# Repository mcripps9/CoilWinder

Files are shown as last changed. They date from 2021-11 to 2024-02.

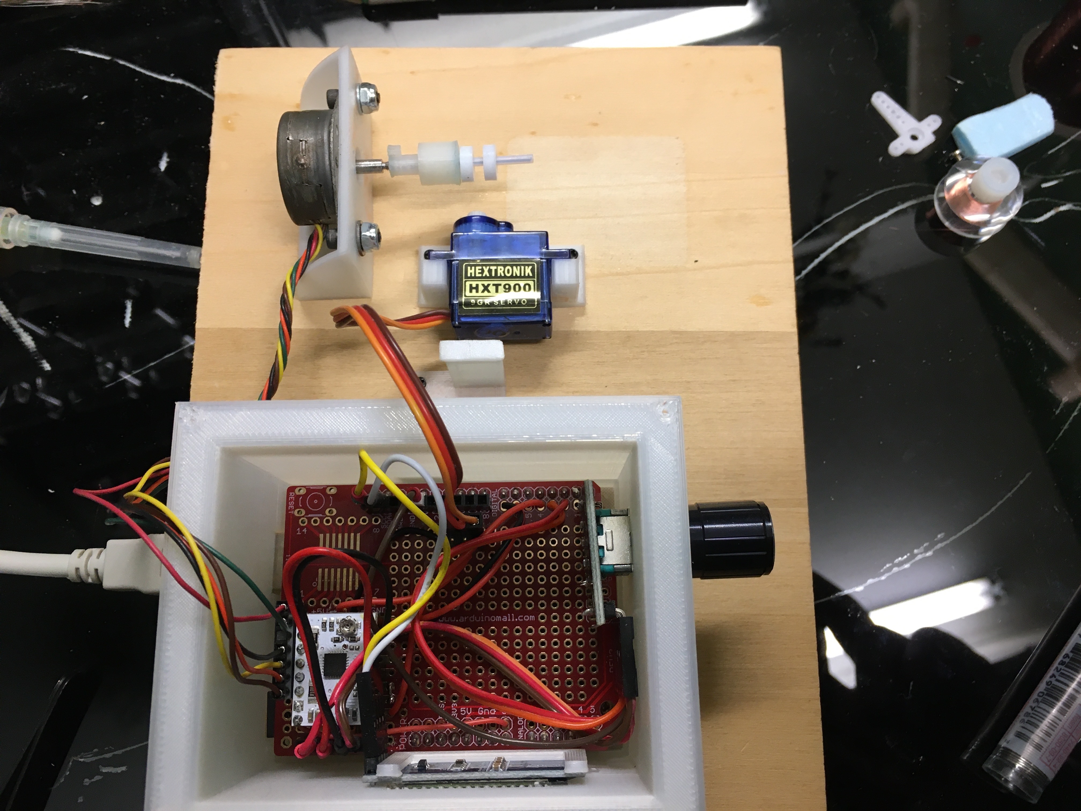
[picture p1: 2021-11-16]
documentation/IMG_1846.jpg

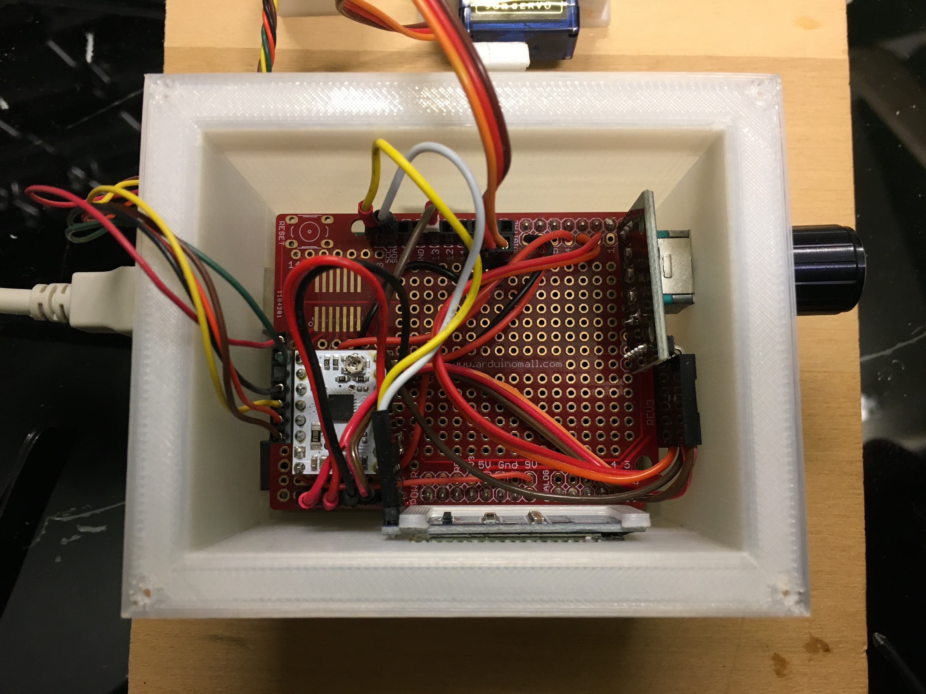
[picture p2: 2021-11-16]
documentation/IMG_1845.jpg

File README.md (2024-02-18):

# CoilWinder
A DIY electronic coil winder built using:
 - Arduino Uno
 - Pololu DRV8834 stepper driver
 - A 5V bipolar stepper motor
 - An optional cheap-o servo
 - 3D printed parts
 - SSD1306 OLED display

Required Arduino libraries:
 - Adafruit BusIO library, version 1.15.0 or later
 - Adafruit GFX library, version 1.11.9 or later
 - Adafruit SSD1306, Version 2.5.9 or later
 - StepperDriver, version 1.4.1 (by Laurentiu Badea)
 - Customized AsyncServoLib - from the libraries directory in this repository

See the documentation folder for a bill of materials and photos of a constructed winder.

See the fusion360 folder for Fusion360 CAD files and STL files for the 3D printed parts

## Installation
- Install the Arduino IDE
- Unzip this project in your ~/Arduino project directory, e.g., $HOME/Documents/Arduino/CoilWinder
- Copy AsyncServoLib from the libraries folder to your ~/Arduino/libraries directory
- Install the remaining Arduino libraries using the Arduino IDE library manager
- Open the CoilWinder.ino file in the Arduino IDE, set the board type to Arduino UNO, compile and upload

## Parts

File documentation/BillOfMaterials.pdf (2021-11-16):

## Hookup

TBD

## Software

- Arduino IDE
- Libraries (installed through Arduino IDE library manager). These versions worked – later versions may work as well:
- Adafruit BusIO library, version 1.7.2
- Adafruit GFX library, version 1.10.6
- Adafruit SSD1306, version 2.4.3
- StepperDriver, version 1.3.1 (by Laurentiu Badea)
- Customized AsyncServoLib.zip from me - unzipped in the Arduino IDE libraries directory
- CoilWinder.zip – unzipped in Arduino projects directory

## Bill of Materials

- Arduino Uno V2 Genuine or suitable clone
- Arduino Protoshield or suitable clone, preferably with pads for at least 18pin DIP IC socket
- https://www.amazon.com/gp/product/B00Q9YB7P
- 16x32 OLED display using SSD1306 I2C driver chip
- https://www.amazon.com/gp/product/B0761LV1SD
- 5V Rotary Encoder Module
- https://www.amazon.com/gp/product/B06XQTHDRR
- Pololu DRV8834 Low-Voltage stepper motor driver carrier or similar clone (use a low-voltage driver that is suitable for +5V motors):
- https://www.pololu.com/product/2134
- https://www.digikey.com/en/products/detail/pololucorporation/2134/10450428
- .1” Female Headers – two 4 pin, two 8 pin and one 10 pin is enough
- (Above Protoshield comes with enough)
- .1” Male header pins – one breakaway strip of 20 or five 4-pin strips is enough
- Hookup wire
- Small stepper motor that will run on 5V at low amperage (100-200ma). Low torque is better than high torque. Stepper will be run in bipolar (4-wire) mode.
- https://www.digikey.com/en/products/detail/sparkfun-electronics/ROB-10551/5766908

- Small servo – as accurate as possible

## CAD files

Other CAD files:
fusion360/CoilWinder.f3d

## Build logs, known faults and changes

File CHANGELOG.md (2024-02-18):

# Change Log
Notable changes to this project are documented here

## v1.1.0

### Added
- Added function to abort "Calibrate Sweep" mode by clicking the button

### Changed
- Changed the mapping of sweep_left and sweep_right values to actual
  servo pulse widths. The values in the coilProgram array range from
  0 to 1400.  These will be normalized to an actual pulse width range using the
  MIN_SERVO and MAX_SERVO constants.  This lets you tweak the servo pulse
  timings globally without having to change the coil programs.
- When scrolling through programs, after a wind is complete, or after
  a wind is aborted the servo will automatically move to the left extent.
- Changed the "Calibrate Sweep" program to a simpler live adjustment of
  the servo position.  Rotate the knob and the servo rotates to match.
  Note down the values of the left and right extents, and you have the
  values for sweep_left and sweep_right
- Removed commented out blocks and other unused code

### Fixed
- Fixed issue where "Calibrate Sweep" program was not program 0 so the
  first program in the list didn't work, but instead ran the Calibrate Sweep
  program.  On power up, program #1 is the default.

## v1.0.0

Initial release

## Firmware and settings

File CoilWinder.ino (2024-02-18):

/*
   Simple stepper motor based coil winder

   Copyright (C)2021, Michael Cripps

   This file may be redistributed under the terms of the Apache 2.0 license.
   A copy of this license has been included with this distribution in the file LICENSE.

   Requires these Arduino libraries:

*/
#include <Arduino.h>
#include <AsyncServoLib.h>
#include <SPI.h>
#include <Wire.h>
#include <Adafruit_GFX.h>
#include <Adafruit_SSD1306.h>

#define	VERSION	"v1.1"

#define SCREEN_WIDTH 128 // OLED display width, in pixels
#define SCREEN_HEIGHT 32 // OLED display height, in pixels

// Declaration for an SSD1306 display connected to I2C (SDA, SCL pins)
// The pins for I2C are defined by the Wire-library.
// On an arduino UNO:       A4(SDA), A5(SCL)
// On an arduino MEGA 2560: 20(SDA), 21(SCL)
// On an arduino LEONARDO:   2(SDA),  3(SCL), ...
#define OLED_RESET     -1 // Reset pin # (or -1 if sharing Arduino reset pin)
#define SCREEN_ADDRESS 0x3C ///< See datasheet for Address; 0x3D for 128x64, 0x3C for 128x32
Adafruit_SSD1306 display(SCREEN_WIDTH, SCREEN_HEIGHT, &Wire, OLED_RESET);

// Output pin for servo
#define SERVO_PIN 9
// this pin should connect to Ground for a button press
#define BUTTON_PIN 13

// Motor steps per revolution. Most steppers are 200 steps or 1.8 degrees/step
#define MOTOR_STEPS 24
// Microstepping mode. If you hardwired it to save pins, set to the same value here.
#define MICROSTEPS 1
// was 16

// Output pins for stepper motor control (STEP and DIR)
#define DIR 6
#define STEP 7

// Input pins for rotary encoder CLK and DT
#define RE_CLK  2
#define RE_DT  3

int counter = 0;
int currentStateCLK;
int lastStateCLK;
String currentDir = "";

// DRV8834 board mimics the A4988
#include "A4988.h"
#define MS1 10
#define MS2 11
#define MS3 12
A4988 stepper(MOTOR_STEPS, DIR, STEP ); //, SLEEP, MS1, MS2, MS3);

AsyncServo asyncServo;
/* 
  Constants defining the input range for the guiding eye servo position.
  These are the ranges of the sweep_left and sweep_right values in the coilProgram array.
  They will be normalized to actual servo pulse width values in us by the AsyncServoLib library
*/
#define MIN_SWEEP 0
#define MID_SWEEP 700
#define MAX_SWEEP 1400
/*
  Constants defining the actual pulse width in us that your servo will tolerate 
  as the minimum (left) position, middle, and maximum (right) position.
*/
#define MIN_SERVO 800
#define MID_SERVO 1500
#define MAX_SERVO 2200

typedef struct
{
  const char *description;  // Text shown on display
  unsigned  spindle_rpm;    // RPM of spindle
  unsigned  sweep_time;     // Time in ms to sweep the guiding eye servo from the left to the right extents
  unsigned  num_winds;      // Total number of winds in the coil
  unsigned  sweep_left;     // Servo pulse width in us of the left extent of the guiding eye servo
  unsigned  sweep_right;    // Servo pulse width in us of the right extent of the guiding eye servo
} COIL;

#define NUM_PROG  12
COIL coilPrograms[NUM_PROG] = {
  {"Calibrate\nSweep", 480, 5000, 10000, MID_SWEEP, MID_SWEEP }, // 1400, 1600
  {"50 AWG\n3x2 75ohm", 250, 19200, 260, 610, 790 },
  {"50 AWG\n3x2 150ohm", 250, 19200, 520, 610, 790 },
  {"44.5 AWG\n3x3 50ohm", 480, 7911, 396, 525, 875},
  {"42.5 AWG\n3x3 40ohm", 480, 6270, 544, 525, 875},
  {"44 AWG\n3x3 150ohm", 100, 13326, 1338, 610, 790},
  {"48 AWG\n3x2 75 ohm", 80, 13326, 328, 610, 790},
  {"48 AWG\n3x3 150ohm", 80, 13326, 645, 610, 790},
  {"48 AWG\n2.4x2 75ohm", 80, 13326, 397, 610, 790 },
  {"42.5 AWG\nSpool", 480, 6270, 10000, 525, 875 },
  {"44 AWG\nSpool", 400, 18459, 10000, 525, 875 }, //7911
  {"49 AWG\nSpool", 60, 13326, 10000, 525, 875}
};

typedef enum { SELECT_MODE, WIND_MODE, CALIBRATE_MODE, PAUSED_MODE } MODE;
typedef enum  {  STARTING, RUNNING, SHIFT_LEFT, SHIFT_RIGHT, PAUSED, ABORTING, DONE } STATE;

typedef struct
{
  const char *description;
  STATE  next_state;
} MENU;

#define NUM_PAUSED_MENU 5
const MENU pauseMenu[NUM_PAUSED_MENU] = {
  {"Paused...", PAUSED },
  {"Press\nto resume", RUNNING },
  {"Shift\nLeft", SHIFT_LEFT },
  {"Shift\nRight", SHIFT_RIGHT },
  {"Press\nto abort", DONE }
};


STATE state = STARTING;
MODE mode = SELECT_MODE;



unsigned calibrate_position = MID_SWEEP;

unsigned program = 1;     // Which program is selected
unsigned menu_item = 0;   // Which menu item is selected (for paused menu)
unsigned wind_count = 0;
unsigned layer_count = 0;
boolean isPaused = false;

void setup() {
  unsigned button_press = 0;

  // Setup Stepper motor driver
  stepper.setEnableActiveState(LOW);
  stepper.disable();
  stepper.setSpeedProfile( stepper.CONSTANT_SPEED, 1, 1 ) ;
  stepper.begin(coilPrograms[program].spindle_rpm, MICROSTEPS);
  
  Serial.begin(115200);
  Serial.println("RESET");

  // Setup OLED display
  // SSD1306_SWITCHCAPVCC = generate display voltage from 3.3V internally
  if (!display.begin(SSD1306_SWITCHCAPVCC, SCREEN_ADDRESS)) {
    Serial.println(F("SSD1306 allocation failed"));
    for (;;); // Don't proceed, loop forever
  }
  display.clearDisplay();
  display.setTextSize(2);
  display.setTextColor(SSD1306_WHITE);
  display.setCursor(0, 0);
  display.println("CoilWinder"); display.println(VERSION);
  display.display();

  // Setup rotary encoder
  pinMode(BUTTON_PIN, INPUT_PULLUP);
  pinMode(RE_CLK, INPUT);
  pinMode(RE_DT, INPUT);
  lastStateCLK = digitalRead(RE_CLK);
  attachInterrupt(0, updateEncoder, CHANGE );
  attachInterrupt(1, updateEncoder, CHANGE );

  // Setup servo
  // The asyncServoLib normalizes the input position to an actual set of pulse widths.
  asyncServo.SetInput( MIN_SWEEP, MID_SWEEP, MAX_SWEEP);     // Max Left, center, and max right extents in coilPrograms
  asyncServo.SetOutput(MIN_SERVO, MID_SERVO, MAX_SERVO);     // Actual left, center, and right pulse widths in us that are sent to servo
  asyncServo.write(coilPrograms[program].sweep_left);
  asyncServo.Attach(SERVO_PIN);
  delay(2000);
  //asyncServo.Detach();

  // Initialize the state machine
  mode = SELECT_MODE;
  state = STARTING;
}

/*
  Interrupt routine that handles rotation of the rotary encoder
*/
void updateEncoder() {
  // Read the current state of RE_CLK
  currentStateCLK = digitalRead(RE_CLK);

  // If last and current state of CLK are different, then pulse occurred
  // React to only 1 state change to avoid double count
  if (currentStateCLK != lastStateCLK  && currentStateCLK == 1){

    switch (mode )
    {
      case PAUSED_MODE:
        // If the DT state is the same as the CLK state then
        // the encoder is rotating CCW so decrement
        if (digitalRead(RE_DT) == currentStateCLK) {
          if ( menu_item == 0 ) {
            menu_item = NUM_PAUSED_MENU;
          }
          menu_item --;
        } else {
        // Encoder is rotating CW so increment
          menu_item ++;
          if ( menu_item >= NUM_PAUSED_MENU ) {
            menu_item = 0;
          }
        }
        break;
      case SELECT_MODE:
        // If the DT state is the same as the CLK state then
        // the encoder is rotating CCW so decrement
        if (digitalRead(RE_DT) == currentStateCLK) {
          if ( program == 0 ) {
            program = NUM_PROG;
          }
          program --;
        } else {
        // Encoder is rotating CW so increment
          program ++;
          if ( program >= NUM_PROG ) {
            program = 0;
          }
        }
        case CALIBRATE_MODE:
        // If the DT state is the same as the CLK state then
        // the encoder is rotating CCW so decrement
        if (digitalRead(RE_DT) == currentStateCLK) {
          if ( calibrate_position == 0 ) {
            calibrate_position = MAX_SWEEP;
          }
          else {
            calibrate_position --;
          }
        } else {
        // Encoder is rotating CW so increment
          calibrate_position ++;
          if ( calibrate_position >= MAX_SWEEP ) {
            calibrate_position = 0;
          }
        }
        break;
    }
  }

  // Remember last CLK state
  lastStateCLK = currentStateCLK;
}

/*
  This routine is called by the AsyncServoLib when the guiding eye hits the left extent.  It tells the asyncServo object
  to start moving towards the right extent
*/
void guidingEye_at_left()
{
  //Serial.print("Left: " );
  //Serial.println(layer_count);
  layer_count++;
  asyncServo.Move(coilPrograms[program].sweep_right, coilPrograms[program].sweep_time, guidingEye_at_right );

}

/*
  This routine is called by the AsyncServoLib when the guding eye hits the right extent.  It tells the asyncServo object
  to start moving towards the left extent
*/
void guidingEye_at_right()
{
  //Serial.println("Right");
  layer_count++;
  asyncServo.Move(coilPrograms[program].sweep_left, coilPrograms[program].sweep_time, guidingEye_at_left );
}

boolean buttonActive = false;


/*
  Wind mode processing loop.  This loop is a state machine that handles different states during a coil wind, including
  when the winding has been paused.

  It handles display updates, checking for button presses, turning the stepper motor on or off, 
  and turning the guiding eye servo on or off.

  Transitions to PAUSE_MODE when the button is pressed, or SELECT_MODE when the coil wind is done
*/
void wind_loop() {
  unsigned wait_time_micros;

  if ( digitalRead( BUTTON_PIN ) == LOW ) {
     buttonActive = true;
  }
  else {
    if ( buttonActive ) {
      asyncServo.Pause();
      mode = PAUSED_MODE;
      isPaused = true;
      buttonActive = false;
      return;
      //GOTO PAUSE MENU
    }
  }

  switch ( state ) {
    case PAUSED:
      isPaused = true;
      mode = PAUSED_MODE;
      display.clearDisplay();
      display.setCursor(0, 0);
      display.println("Paused");
      display.println(wind_count);
      display.display();
      break;
    case SHIFT_LEFT:
      coilPrograms[program].sweep_left -= 5;
      coilPrograms[program].sweep_right -= 5;
      state = RUNNING;
      break;
    case SHIFT_RIGHT:
      coilPrograms[program].sweep_left += 5;
      coilPrograms[program].sweep_right +=5 ;
      state = RUNNING;
      break;
    case STARTING:
      wind_count = coilPrograms[program].num_winds;
      display.clearDisplay();
      display.setCursor(0, 0);
      display.println("Starting");
      display.println(wind_count);
      display.display();
      Serial.println("START");
      asyncServo.write(coilPrograms[program].sweep_left);
      asyncServo.Attach(SERVO_PIN);
      stepper.begin(coilPrograms[program].spindle_rpm, MICROSTEPS);
      stepper.enable();
      guidingEye_at_left();
      stepper.startRotate(360);
      state = RUNNING;
      break;
    case RUNNING:
      if ( isPaused == true ) {
        asyncServo.Resume();
        isPaused = false;
      }
      wait_time_micros = stepper.nextAction();
      if (wait_time_micros <= 0) {
        stepper.startRotate( 360 );
        wind_count--;
        //Serial.print("Layer: ");
        //Serial.print(layer_count);
        //Serial.print(" Wind: ");
        //Serial.println(wind_count);
        display.clearDisplay();
        display.setCursor(0, 0);
        display.println(wind_count);
        display.display();
      }
      if ( isPaused == true ) {
        asyncServo.Resume();
        isPaused = false;
      }
      asyncServo.Update();

      if ( wind_count <= 0  ) {
        state = DONE;
      }
      break;
    case DONE:
      stepper.disable();
      asyncServo.Stop();
      asyncServo.write( coilPrograms[program].sweep_left );
      Serial.println("Done");
      display.clearDisplay();
      display.setCursor(0, 0);
      display.println("Done!");
      display.display();
      delay(5000);
      state = STARTING;
      mode = SELECT_MODE;
      asyncServo.Detach();
      buttonActive = false;
      break;
  }
}

/*
  Calibrate mode processing loop.  This mode is used to determine the exact values for the left and right extents of the
  guiding eye to be used as the 'sweep_left' and 'sweep_right' values in the coilPrograms coil program.

  The value on the display is the current servo position in microseconds.

  Clicking the button will stop calibration mode and go back to the main menu.
*/
void calibrate_loop()
{
  unsigned wait_time_micros = 0;

  if ( digitalRead( BUTTON_PIN ) == LOW ) {
     buttonActive = true;
  }
  else {
    if ( buttonActive ) {
      asyncServo.Pause();
      mode = WIND_MODE;
      state = DONE;
      buttonActive = false;
      return;
      //GOTO WIND_MODE and stop the program
    }
  }
  switch ( state )
  {
    case STARTING:
      display.clearDisplay();
      display.setCursor(0, 0);
      display.println("Calibrating.....");
      display.display();
      Serial.println("START Calibrate");
      delay(1000);
      asyncServo.write(0);
      asyncServo.Attach(SERVO_PIN);
      //stepper.begin(coilPrograms[program].spindle_rpm, MICROSTEPS);
      //stepper.enable();
      //guidingEye_at_left();
      //stepper.startRotate(360);
      state = RUNNING;
      break;
    case RUNNING:
      //wait_time_micros = stepper.nextAction();
      //if (wait_time_micros <= 0) {
      //  stepper.startRotate( 360 );
      //}
      asyncServo.write( calibrate_position );
      display.clearDisplay();
      display.setCursor(0, 0);
      display.println(asyncServo.GetCurrentPosition());
      display.display();
      //if ( old_state == PAUSED || old_state == ABORTING ) {
      //  asyncServo.Resume();
      //}
      //asyncServo.Update();
      break;
  }
}

/*
  Main menu processing loop.  Scroll through the programs with the knob, and listen for button press events
  to select the program and start a wind, or to enter calibration mode to get the values for the guiding eye extents

  Transitions to either WIND_MODE for a coil wind for CALIBRATE_MODE to calibrate the guiding eye extents
*/
void select_loop()
{
    if ( digitalRead( BUTTON_PIN ) == LOW ) {
      if ( buttonActive == false ) {
        buttonActive = true;
        Serial.println( "Button pressed");
        //buttonTimer = millis();
      }
    }
    else {
      if ( buttonActive == true ) {
        buttonActive = false;
        Serial.println( "Button released" );
        if ( program == 0 ) {
          mode = CALIBRATE_MODE;
        }
        else {
          mode = WIND_MODE;
        }
        state = STARTING;
      }
    }
    display.clearDisplay();
    display.setCursor(0, 0);
    display.println(coilPrograms[program].description);
    asyncServo.write(coilPrograms[program].sweep_left);
    display.display();
}

/*
  Puased menu processing.  Scroll through the paused menu options, and check for button presses.
  The paused menu is invoked when you click the button during a winding program, and lets you either abort the
  wind, or slide the guiding eye extents left or right if your widing form is not correctly aligned to the guiding eye.

  Transitions back to WIND_MODE after a button click.
*/
void paused_loop()
{
    if ( digitalRead( BUTTON_PIN ) == LOW ) {
      if ( buttonActive == false ) {
        buttonActive = true;
        Serial.println( "Button pressed");
        //buttonTimer = millis();
      }
    }
    else {
      if ( buttonActive == true ) {
        buttonActive = false;
        Serial.println( "Button released" );
        state = pauseMenu[menu_item].next_state;
        mode = WIND_MODE;
        menu_item = 0;
      }
    }
    display.clearDisplay();
    display.setCursor(0, 0);
    display.println(pauseMenu[menu_item].description);
    display.display();
}

void loop()
{
  switch ( mode )
  {
    // Mode when selecting the program
    case SELECT_MODE:
      select_loop();
      break;
    // Mode when paused during a program (invoked by clicking the button)
    case PAUSED_MODE:
      paused_loop();
      break;
    // Mode when a coil is being wound
    case WIND_MODE:
      wind_loop();
      break;
    // Mode used by program 0 to calibrate the guiding eye sweep extents
    case CALIBRATE_MODE:
      calibrate_loop();
      break;
  }
}

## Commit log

2024-02-18 Bug fixes and updates for v1.1.0
    [CoilWinder.ino]
2024-03-10 Added speedy knob rotate and fixed Reboot
    [CoilWinder.ino]
